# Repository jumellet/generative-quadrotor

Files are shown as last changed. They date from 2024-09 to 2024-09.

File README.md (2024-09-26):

# Modular Quadrotor

This repository contains the files necessary for building the quadrotor presented in the paper called "Simplifying Quadrotor Frame Design: Toward Scalability with a Modular Robot". The ultimate objective is to improve reproducibility in aerial robotics, by providing a modular robot. It can be manufactured easily and adapted to any research need. 

Freeflight           |  Quadrotor components
:-------------------------:|:-------------------------:
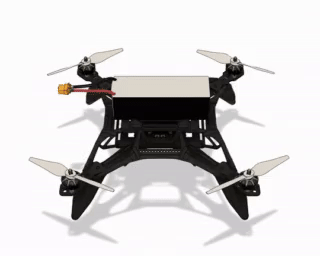
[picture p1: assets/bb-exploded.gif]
  |  

## Key Features
- *Lightweight Structure*: Optimized design reduces the frame's overall weight, enhancing flight efficiency.
- *Modular and Adaptable*: The frame is compatible with a wide variety of components and payload configurations, making it ideal for different aerial manipulation tasks.
- *Simplified Assembly*: Fewer parts and an intuitive design allow for faster and easier assembly and disassembly, reducing maintenance time.
- *Open-Source Design*: The frame and complementary parts are provided under an open-source license, allowing for community contributions and modifications

## Quadrodor components

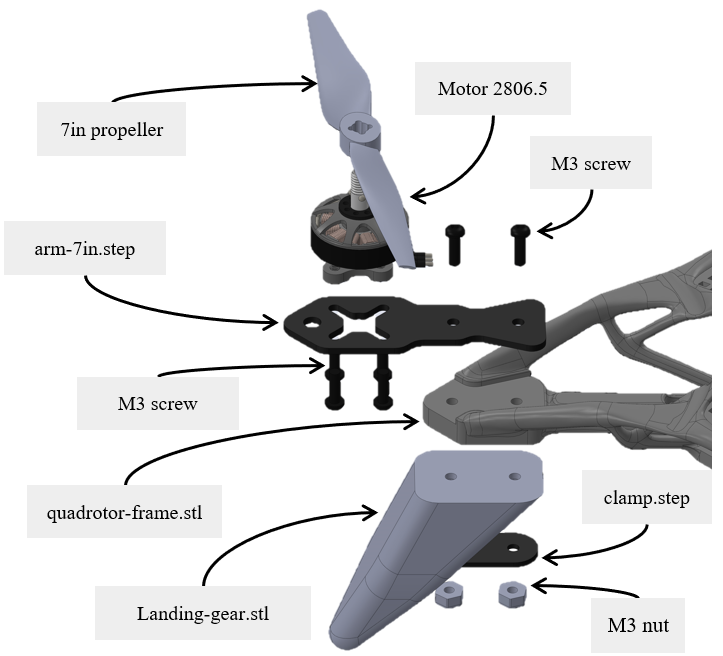
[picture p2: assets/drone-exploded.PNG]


The aerial robots is composed of a reduced number of components that are described below.

### 3D print

For resilience against impoact we experienced better result at using PETG for the frame, and TPU for the landing gear. The frame must be printed with support. We observed better quality printing with Tree shape support, while the landing gear does not require any.

- [Frame](parts/frame/quadrotor-frame.stl)
- [Landing gears](parts/landing-gear/landing-gear.stl) x 4

### CNC cut

Because plastic from additive manufacturing techniques have been experienced melting with motors heat, we decide to CNC cut sheets of carbon fiber. It allows to diffuse heat and is easy to mount. We also provided a universal shape that permits to mount the vast majority of brushless motors. Also, we provide several lengths to be used with different propellers size.

- [Arm](/parts/arm/) of 3mm thickness x 4
- [Clamp](/parts/arm/clamp.step) of 1mm thickness x 4
- M3 L16 bolts x 8

The arm is linked with only two bolts and attach the landing gear with the frame thanks to the clamp.

### Electronics

To command the robot we connect the flight controller and flash it with the last version of [PX4](https://github.com/PX4/PX4-Autopilot). Motor depending on the application can be mounted with four screws.

- Pixhawk 6C
- Brushless motors x 4
- M3 L6 x 16

## Accessories

Here we propose two accessories to be mounted on the quadrotor for experimentation:

- [Manipulator stick](parts/manipulator-stick/)
- Motion capture [markers supports](parts/marker-attach/)

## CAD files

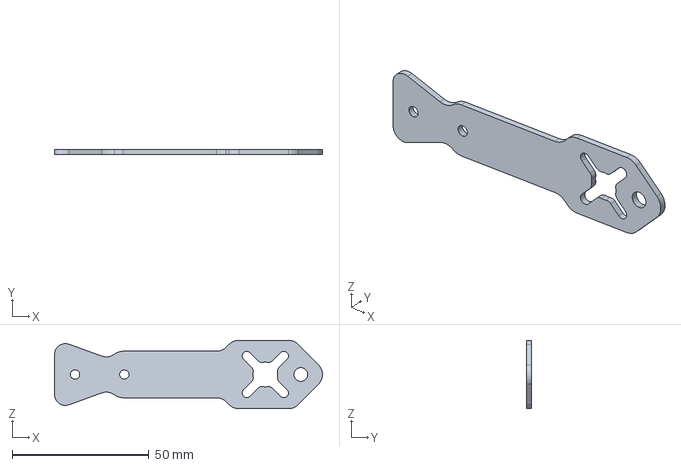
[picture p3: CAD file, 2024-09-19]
parts/arm/arm-9in.step
97.9 x 2.00 x 25.0 mm

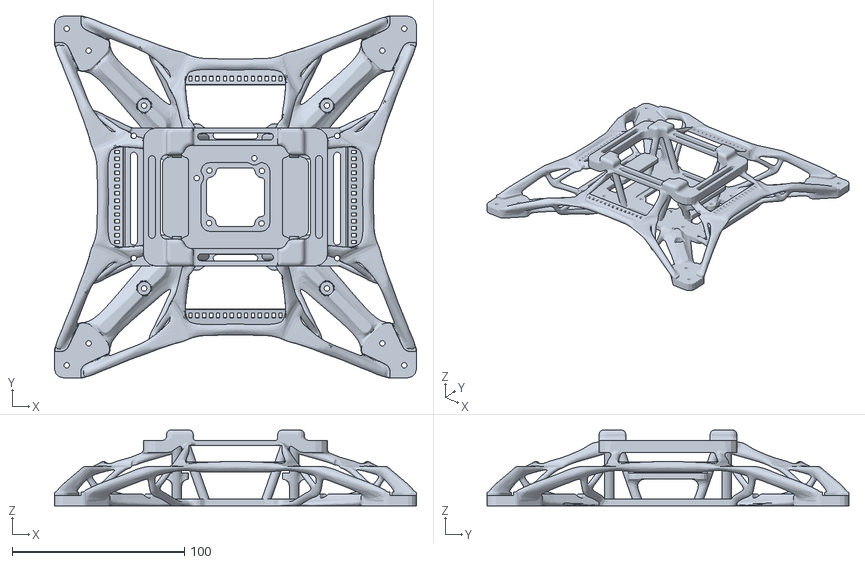
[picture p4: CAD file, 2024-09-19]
parts/frame/quadrotor-frame.stl
210.1 x 209.9 x 44.0

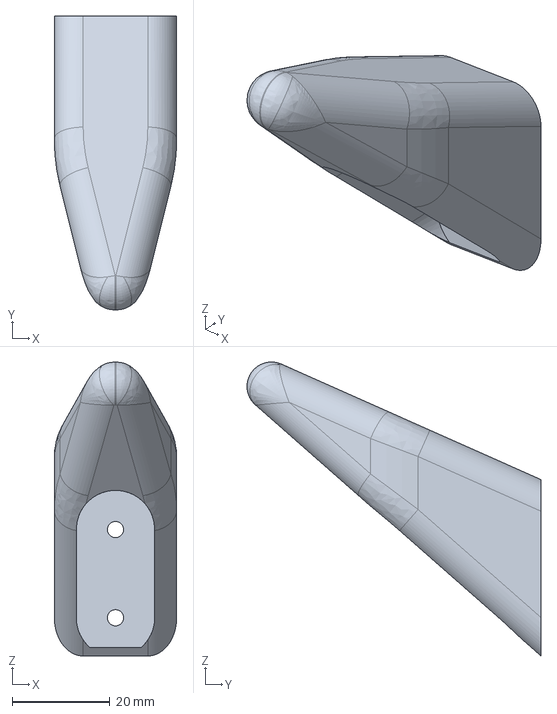
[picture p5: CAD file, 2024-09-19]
parts/landing-gear/landing-gear.step
25.0 x 60.0 x 60.0 mm

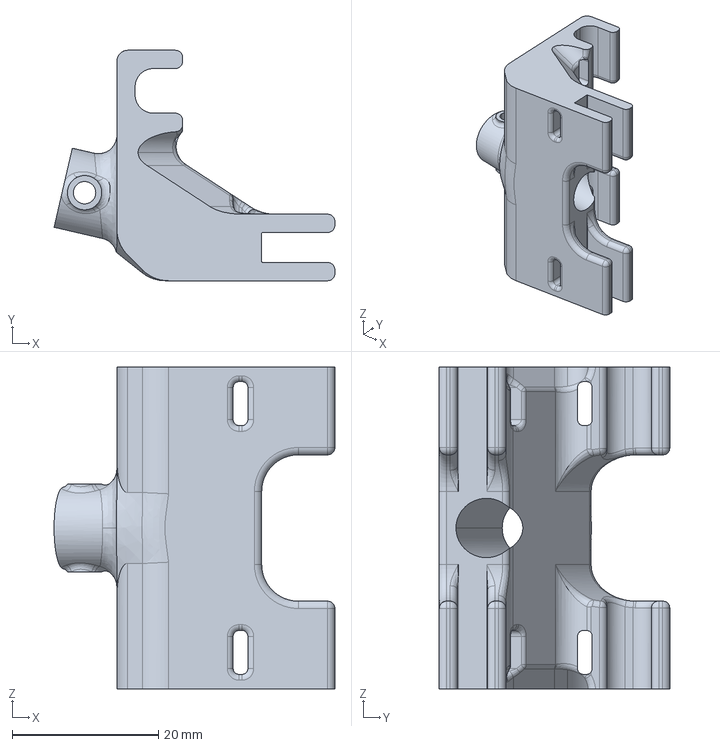
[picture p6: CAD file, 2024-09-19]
parts/manipulator-stick/stick-support.step
38.4 x 31.5 x 44.0 mm

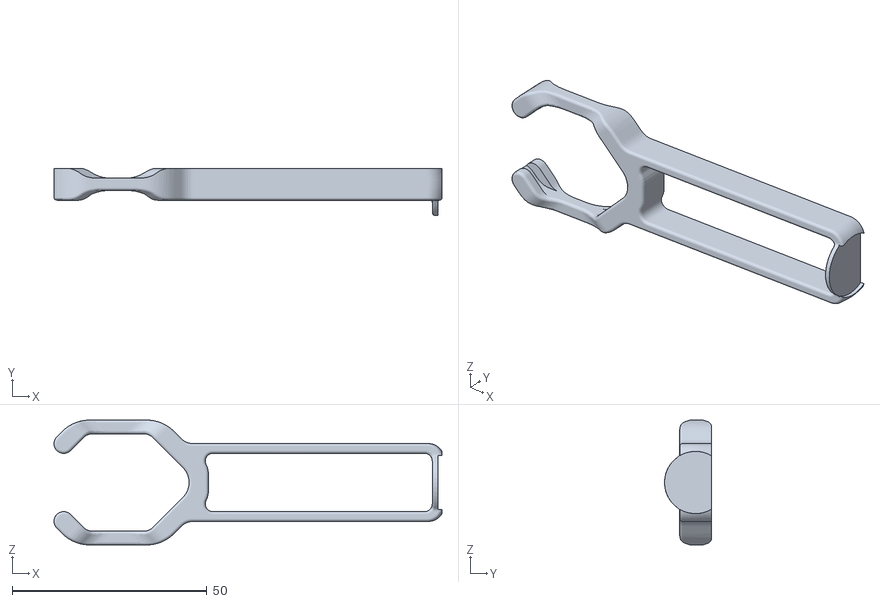
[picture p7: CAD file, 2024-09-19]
parts/marker-attach/marker-attach-60.stl
99.7 x 12.1 x 32.1

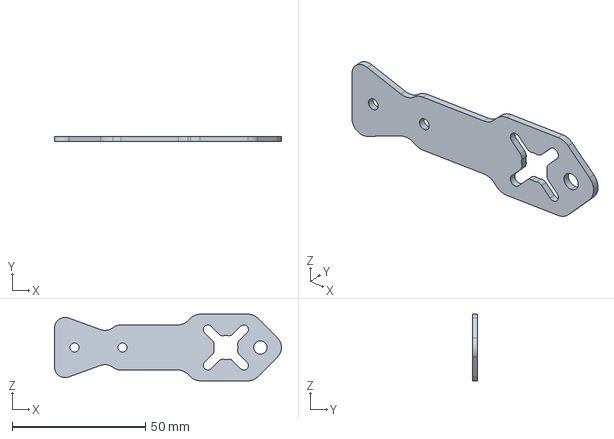
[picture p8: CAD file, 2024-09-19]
parts/arm/arm-8in.step
85.2 x 2.00 x 25.0 mm

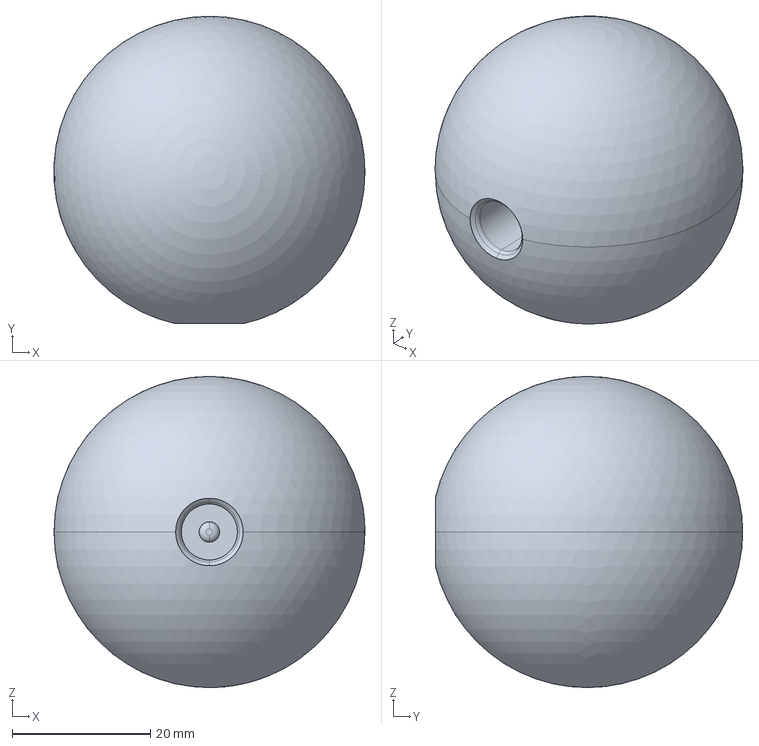
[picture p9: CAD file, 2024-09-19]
parts/manipulator-stick/end-effector-stick.step
45.0 x 44.5 x 45.0 mm

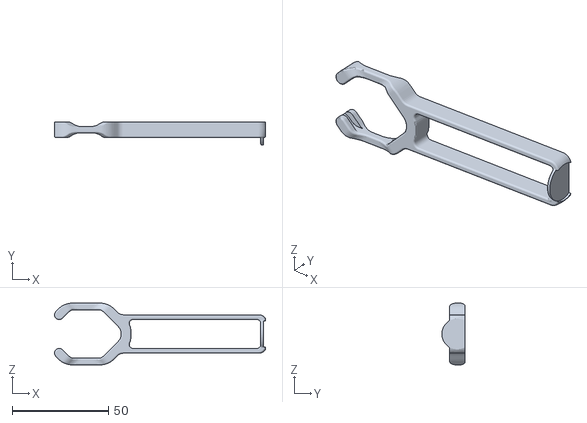
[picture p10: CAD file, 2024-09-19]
parts/marker-attach/marker-attach-70.stl
109.7 x 12.1 x 32.1

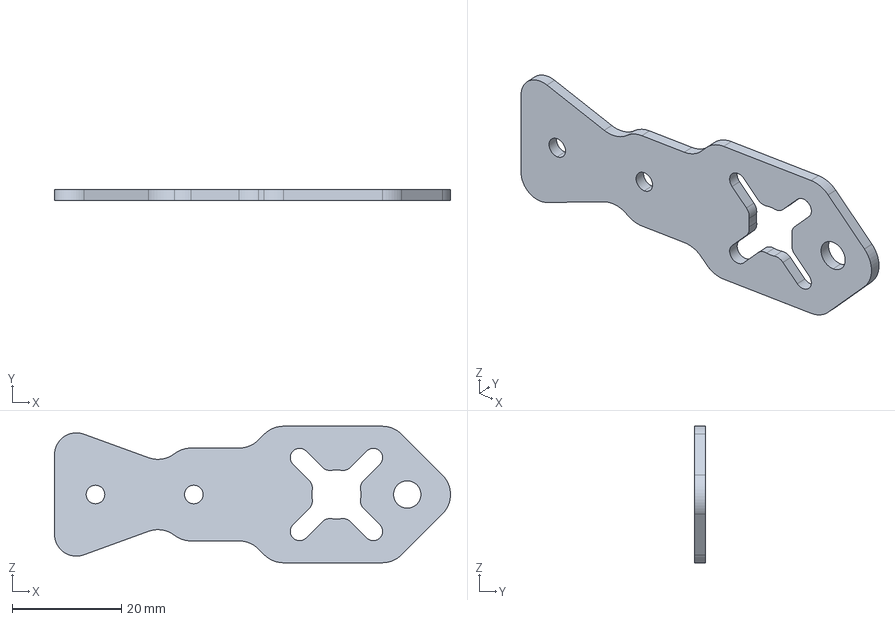
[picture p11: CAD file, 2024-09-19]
parts/arm/arm-7in.step
72.5 x 2.00 x 25.0 mm

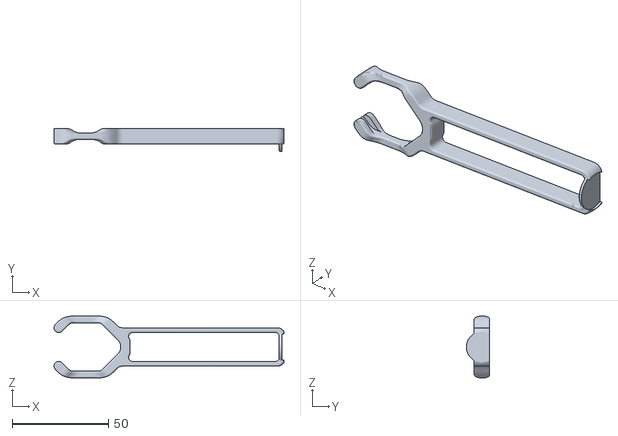
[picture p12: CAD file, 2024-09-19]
parts/marker-attach/marker-attach-80.stl
119.7 x 12.1 x 32.1

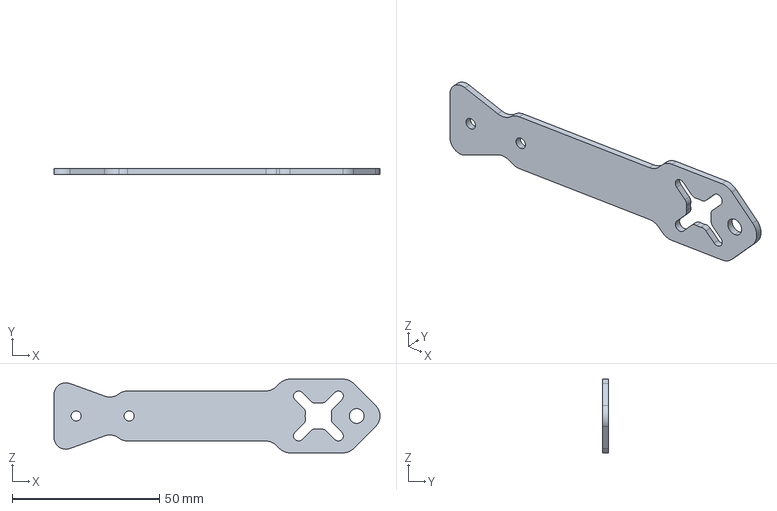
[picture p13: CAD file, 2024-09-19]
parts/arm/arm-10in.step
110.6 x 2.00 x 25.0 mm

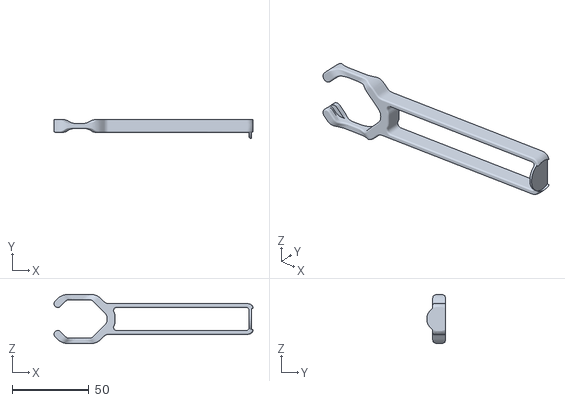
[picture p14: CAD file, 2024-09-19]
parts/marker-attach/marker-attach-90.stl
129.7 x 12.1 x 32.1

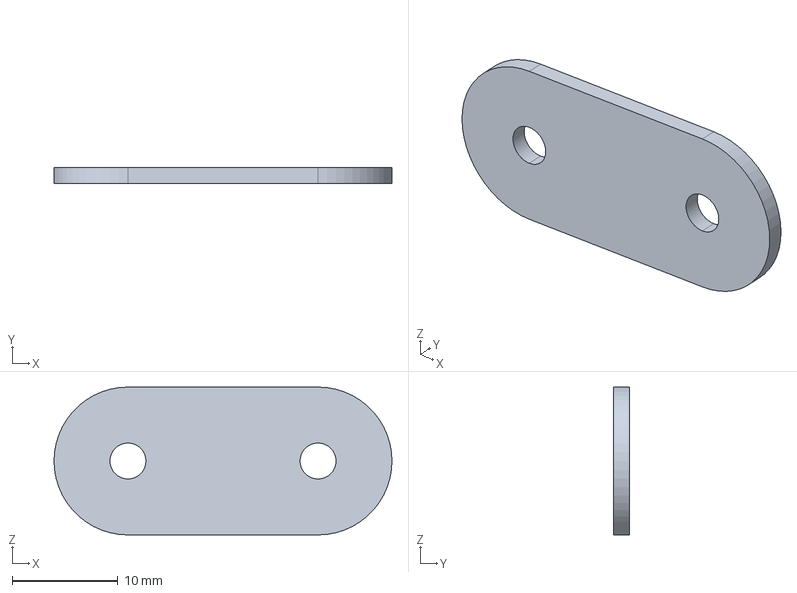
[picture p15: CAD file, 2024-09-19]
parts/arm/clamp.step
32.0 x 1.50 x 14.0 mm

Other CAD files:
parts/landing-gear/landing-gear.stl

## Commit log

2024-09-19 Add stick for push-and-slide
    [end-effector-stick.step, stick-support.step]
2024-09-19 Add frame
    [quadrotor-frame.stl]
2024-09-19 Add landing gear
    [landing-gear.step, landing-gear.stl]
2024-09-19 Add arms and clamp
    [arm-10in.step, arm-7in.step, arm-8in.step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]
2024-09-19 Add marker attach
    [marker-attach-60.stl, marker-attach-70.stl, marker-attach-80.stl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]
